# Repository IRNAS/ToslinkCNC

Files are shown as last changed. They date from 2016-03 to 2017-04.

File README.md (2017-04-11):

# ToslinkCNC

CNC machine is usually controlled via parallel bus, containing six signals. For each of the three axes there are two signals: STEP and DIR. At each positive edge of the STEP signal, the corresponding stepper motor moves into direction set by DIR signal. In addition to these six signals, there can also be other general purpose control signals.

Parallel bus on longer distances and in noisy environment can be susceptible to electromagnetic interferences. Because of this we decided to design an interface to transport these parallel signals via an optical link. For successful transfer via optical fiber the first thing that must be done is to convert parallel data to serial bit stream. Moreover, because of the inherent design of optical transmitters and receivers, serial data must also be Manchester encoded.

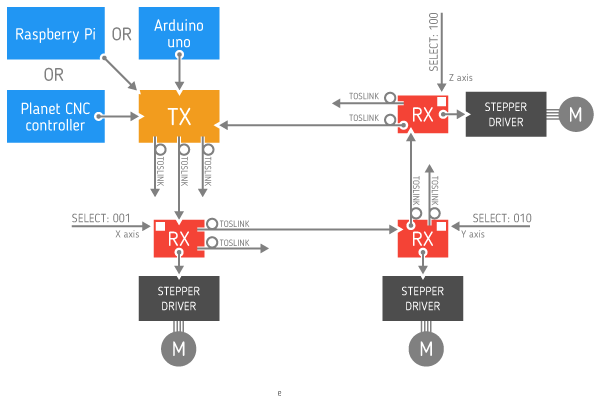
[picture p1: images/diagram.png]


Our design is based on [Serializer / Deserializer for Audio Fiber Optic](http://opencores.org/project,parallel_io_through_fiber) project published on Open Cores. 

## Use cases
ToslinkCNC has been developed for use with [GoodenoughCNC Plasma](http://goodenoughcnc.eu) cutter as our answer to continuous problems with electrical noise and interference. The following configuration is used in the system. 

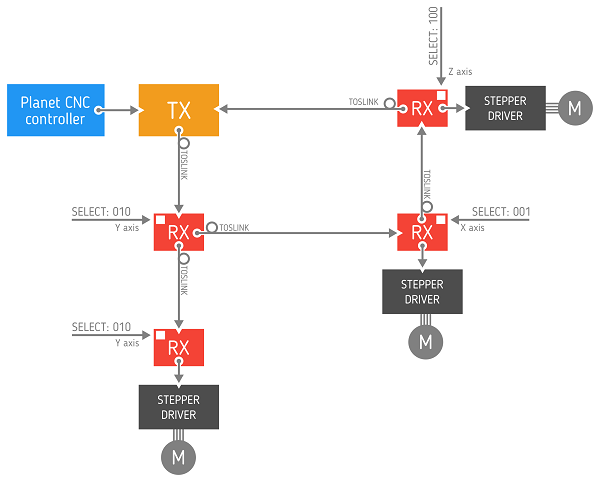
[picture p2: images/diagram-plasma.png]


## Toslink Receiver-transceiver

For each motor on the CNC machine there is one PCB, containing Toslink receiver. Receiver PCB, together with motor driver, can be mounted on the motor. Receiver is being used with [PoLabs' PoStep25-32 stepper motor driver](http://www.poscope.com/PoStep25-32). PCB is being powered through motor driver connector using +5V. To enable this the +5V supply from motor driver should be connected to unused 9th pin on the driver's IDC connector usign a piece of insulated wire. PCB consists of one CPLD, two optical transmitters, one optical receiver, one DIP switch for selecting the axis and one limit switch / trigger connector. Limit switch is insulated through an optocoupler and trigger output is open drain type. Toslink transmitter DLT1111 and Toslink receiver DLR1111 were used, which enable data transfer speed up to 16 Mbps. We used Xilinx XC9572XL CPLD to implement the necessary logic for protocol conversion. Receivers can also be connected in daisy chain.

### Using IDC-10 connector:
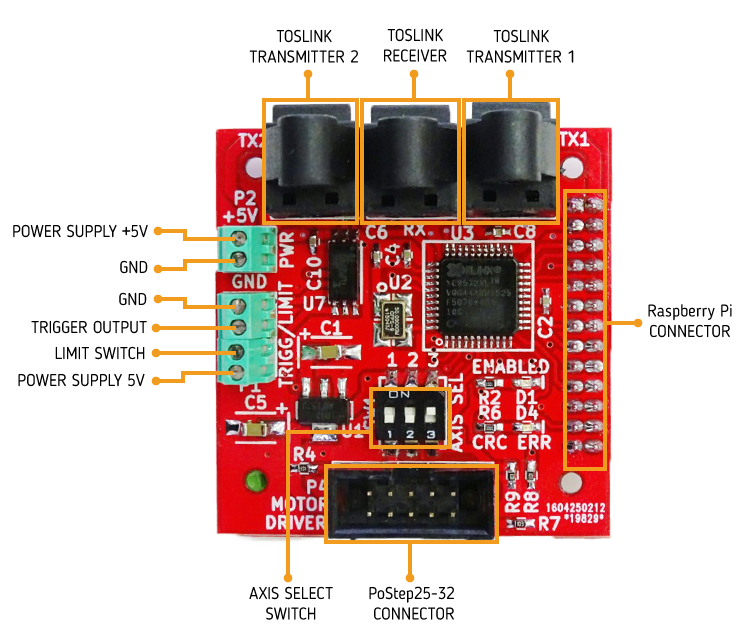
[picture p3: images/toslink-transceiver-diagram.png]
toslink-cnc-1


### Using terminal blocks:
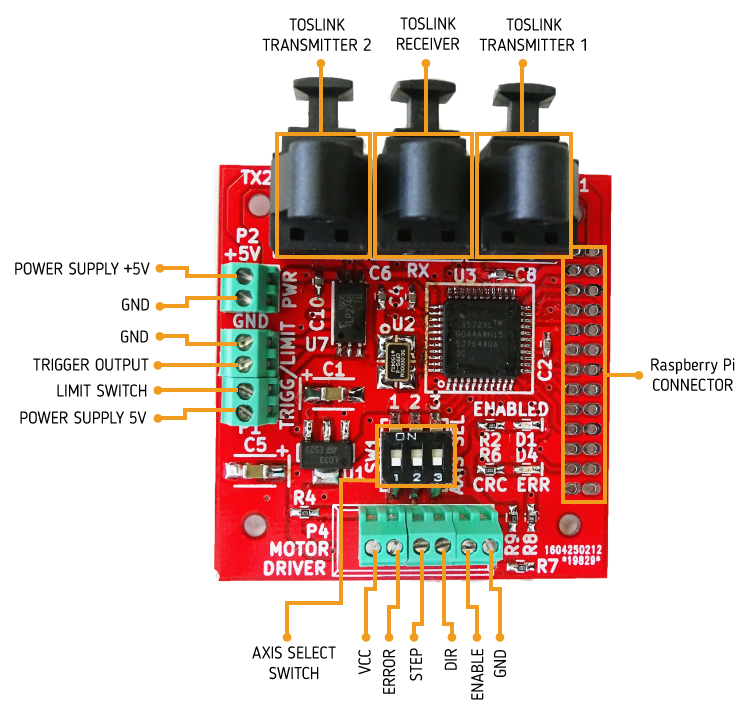
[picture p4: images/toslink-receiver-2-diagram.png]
toslink-cnc-1-1


## Toslink Transmitter

Transmitter consists of two PCBs, an Arduino sield and a Toslink transciever. Both PCBs are stacked together. Toslink transciever PCB is identical to one used for receiver. Arduino shield consists of headers for Arduino and connectors for [CNC USB Controller Mk3/4 from Planet CNC](http://www.planet-cnc.com/index.php?page=hardware) and PoStep25-32 driver. There is also a terminal block for connecting limit switches and trigger signals. Circuit can be powered either through terminal block (+5V), through Arduino Uno if attached as a shield, or from Planet CNC Controller.

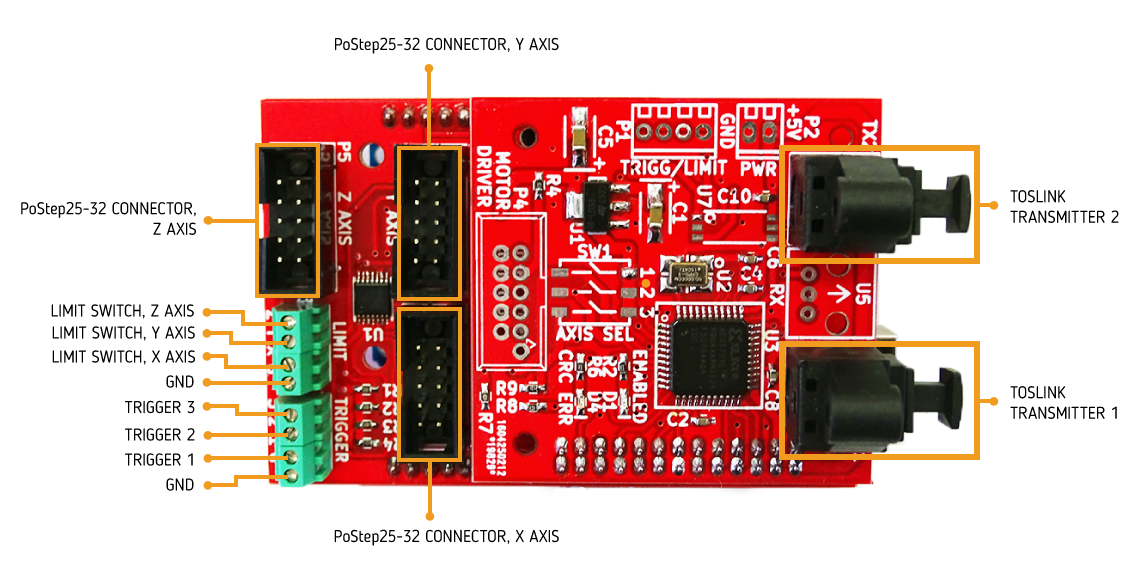
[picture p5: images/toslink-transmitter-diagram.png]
toslink-cnc-1-2


## Toslink Transmitter / Arduino Shield

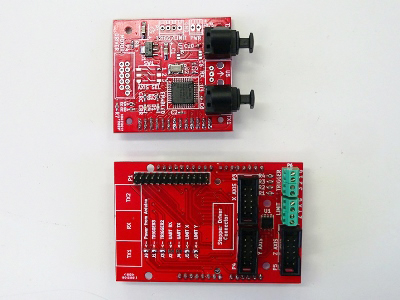
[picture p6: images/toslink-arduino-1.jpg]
toslink-cnc-2

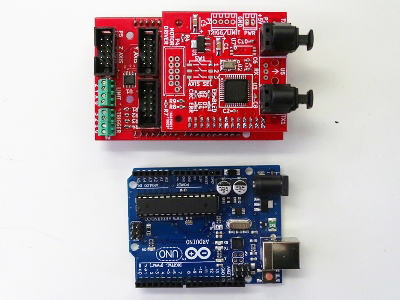
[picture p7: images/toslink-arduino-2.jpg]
toslink-cnc-3

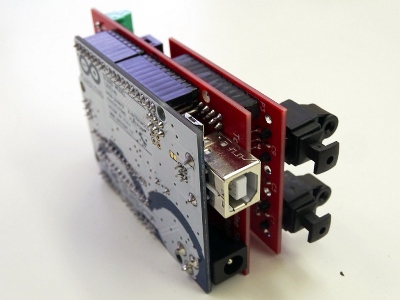
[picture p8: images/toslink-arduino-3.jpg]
toslink-cnc-4


## Toslink Transmitter / Planet CNC

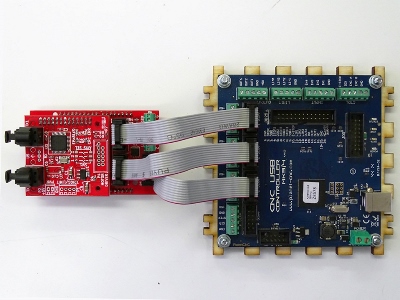
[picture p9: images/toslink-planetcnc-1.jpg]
toslink-cnc-5

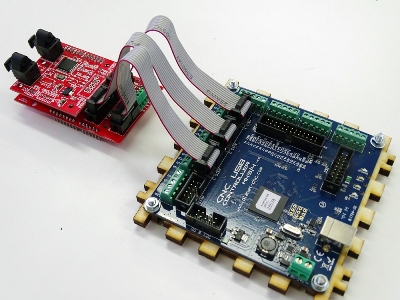
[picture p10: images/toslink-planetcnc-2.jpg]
toslink-cnc-6


## Toslink Transmitter / Raspberry Pi Shield

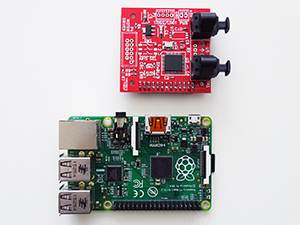
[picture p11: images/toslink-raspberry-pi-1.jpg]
toslink-cnc-7

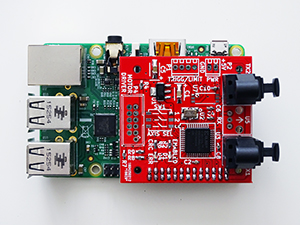
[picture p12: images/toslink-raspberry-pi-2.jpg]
toslink-cnc-8


## Firmware Description

All data is being transmitted in frames of fixed length. Frames are transmitted without gaps between them. Each frame contains 3 direction values, 3 step values, vaule of enable signal, 3 values of limit/end switch signals (these fields are being shared with 3 trigger values), parity bits and frame delimiter. To detect parity bit corruption, both even and odd parity bits are being transmitted. Transmitter places direction, step, enable and trigger values in new frame, adds calculated parity bits and sends the frame to the first receiver in daisy chain. Receiver reads the enable value and direction, step and trigger values ( based on axis selection). Receiver replaces the correspondig trigger value with limit switch value, calculates new parity bits and sends this new frame to the next receiver in dasy chain. Output of the last receiver in dasy chain is connected to transmitter input. Transmitter reads all three limit switch values from received frame.

frame-structure

Data in optical fiber is manchester encoded. For logic '0', logic '1' and frame delimiter three different patterns are being used. They were selected so that all of them have the same length and are completely different from each other. Decoding is based on time elapsed between two rising edges of clock. If elapsed time is shorter than 12 clock cycles, receiver decodes it as a short step. If it's longer than 12 and shorter than 20 clock cycles, then it's decoded as a medium step. If elapsed time is longer than 20 clock cycles, it's decoded as a long step.

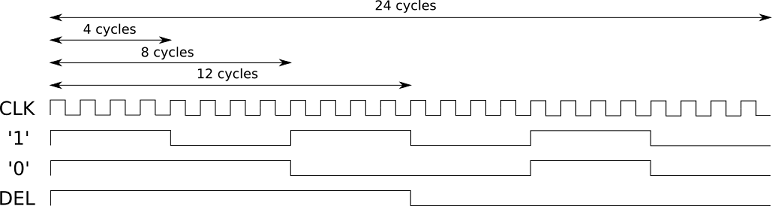
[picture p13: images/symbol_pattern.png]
symbol-pattern


Main transmitter module consists of a step sampler and an optical transmitter. Step sampler samples and shapes incomming step, direction, enable and trigger signals and passes them forward to the optical transmitter. Optical transmitter handles data framing, manchester encoding and sends encoded data to Toslink transmitter.

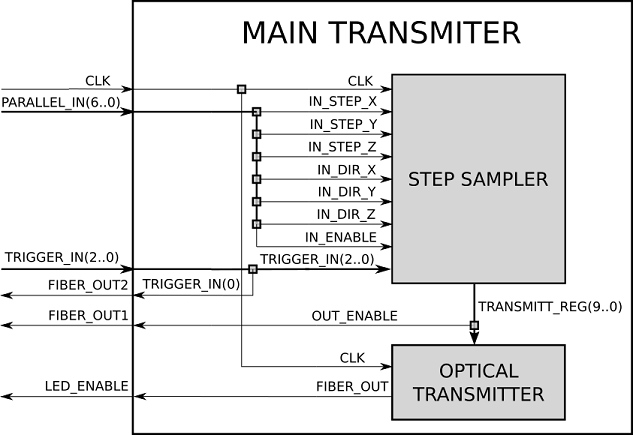
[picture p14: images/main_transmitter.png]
main-transmitter-module


Block diagram of step sampler is presented in figure below:

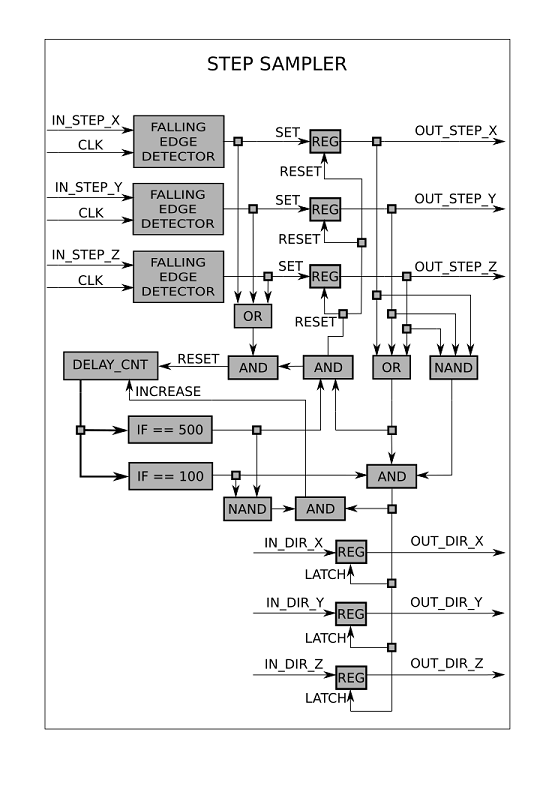
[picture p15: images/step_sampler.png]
step-sampler


Optical transmitter consists of shift register and manchester encoder. Shift register block diagram is presented in figure below:

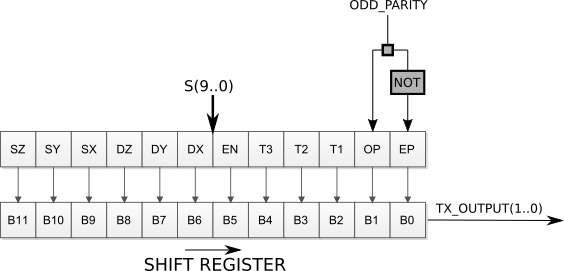
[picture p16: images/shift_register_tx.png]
shift-register-tx


Manchester encoder consists of three look-up tables and one multiplexer. If value of *tx_output* is "00" the '0' pattern, if  "01" the '1' pattern and if "10" the DEL pattern is generated on the output.

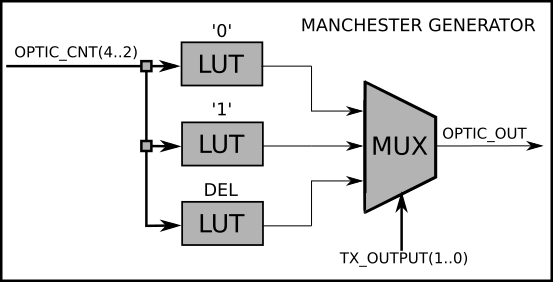
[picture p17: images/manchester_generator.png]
manchester-encoder


Main receiver module consists of an optical receiver and a step generator. Optical receiver accepts signal from Toslink receiver, decodes it and passes extracted data to step generator. It also adds limit signal values, calculates new parity, manchester encodes data and passes it foward to both Tolsink transmitters. Step generator correctly shapes the received signals.

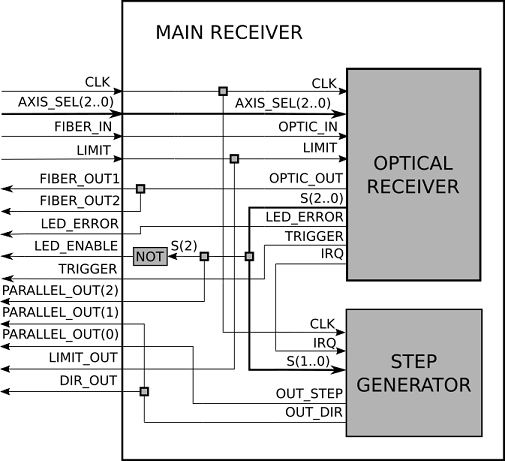
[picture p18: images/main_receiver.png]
main-receiver-module


Optical receiver consists of manchester decoder, shift register and manchester encoder (which is identical to the one used in transmitter). Block diagram of receiver shift register is presented in figure below:

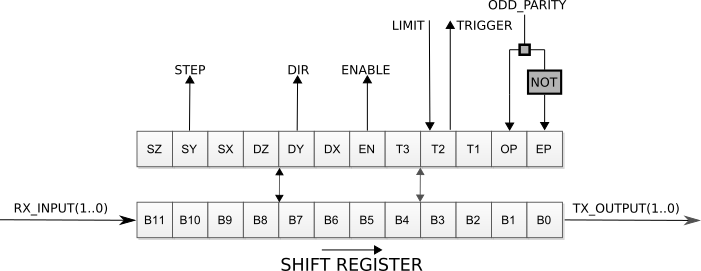
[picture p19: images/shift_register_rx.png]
shift-register-rx


Manchester decoder consists of a simple low-pass filter and a step sampler.

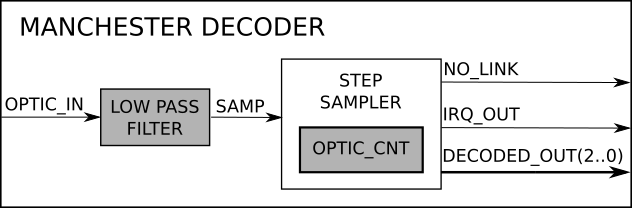
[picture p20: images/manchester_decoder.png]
manchester-decoder


Step sampler is a finite state machine. It's diagram of possible states is presented in figure below. Movement between states is based on received step width: short, medium or long. If step width is too long, the connection is lost and motor driver is disabled (enable signal equals to '1'). As soon as the correct manchester symbol is received, the connection is again established.

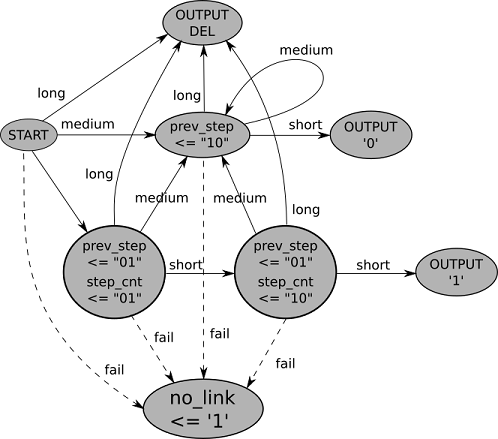
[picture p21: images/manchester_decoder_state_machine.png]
manchester-decoder-state-machine


## Known Isues

 * There is not enough room on the CPLD to hold both, the transmitter and the receiver. To enable transfer of limit switch signals from receivers back to transmitter, there would also need to be an additional optical receiver implemented on the transmitter PCB's CPLD. This problem can be solved by stacking two transcievers one over another. Firmware for the second transciever is available in [Transmitter](Transmitter/return path receiver CPLD VHDL code) folder.

---

#### License

All our projects are as usefully open-source as possible.

Hardware including documentation is licensed under [CERN OHL v.1.2. license](http://www.ohwr.org/licenses/cern-ohl/v1.2)

Firmware and software originating from the project is licensed under [GNU GENERAL PUBLIC LICENSE v3](http://www.gnu.org/licenses/gpl-3.0.en.html).

Open data generated by our projects is licensed under [CC0](https://creativecommons.org/publicdomain/zero/1.0/legalcode).

All our websites and additional documentation are licensed under [Creative Commons Attribution-ShareAlike 4 .0 Unported License] (https://creativecommons.org/licenses/by-sa/4.0/legalcode).

What this means is that you can use hardware, firmware, software and documentation without paying a royalty and knowing that you'll be able to use your version forever. You are also free to make changes but if you share these changes then you have to do so on the same conditions that you enjoy.

Koruza, GoodEnoughCNC and IRNAS are all names and marks of Institut IRNAS Rače. 
You may use these names and terms only to attribute the appropriate entity as required by the Open Licences referred to above. You may not use them in any other way and in particular you may not use them to imply endorsement or authorization of any hardware that you design, make or sell.

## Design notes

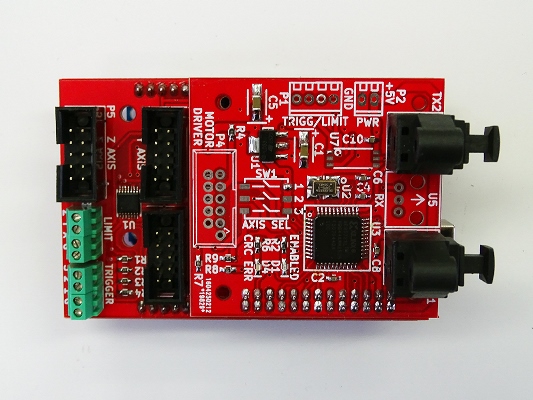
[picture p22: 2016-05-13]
images/transmitter-pinout.jpg

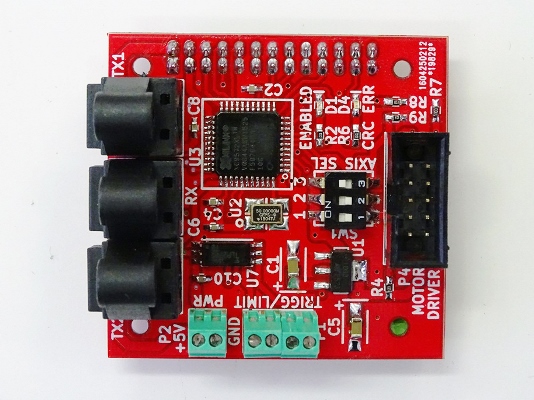
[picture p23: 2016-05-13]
images/transceiver-pinout.jpg

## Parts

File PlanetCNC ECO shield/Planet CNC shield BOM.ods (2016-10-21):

Designator | Package | Quantity | Description
P1 | Toslink CNC Transciever | 1 | Toslink CNC Transciever
P2 | Planet CNC ECO | 1 | Planet CNC ECO
P3 | terminal block, 2.5mm, 2-pole | 1 | term block 2

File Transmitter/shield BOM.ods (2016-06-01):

Designator | Package | Quantity | Description
P2 | Toslink CNC Transciever | 1 | Toslink CNC Transciever
P1 | Arduino UNO | 1 | Arduino UNO
P3,P4,P5 | male IDC 10 | 3 | PoStep25-32 connector
P6,P7 | terminal block, 2.5mm, 4-pole | 2 | term block 4
R1,R2,R3,R4 | R0603 | 4 | 10K

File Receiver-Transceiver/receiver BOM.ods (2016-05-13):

Designator | Package | Quantity | Description
P3 | female header straight, 2x13, 2.54mm | 1 | RPI header
P4 | male IDC 10 | 1 | PoStep25-32 connector
U4,U6 | DLT1111 | 2 | Toslink transmitter
U5 | DLR1111 | 1 | Toslink receiver
U3 | VQFP44 | 1 | XC9572XL
U1 | SOT-223 | 1 | TLV1117, 3.3V
C9,C8,C7,C6,C4,C3,C2,C10 | C0603 | 8 | 100nF,25V
C5,C1 | tantal capacitor, size B | 2 | 10uF,25V
U2 | TCXO 5x3.2 mm | 1 | CFPS-9-50M, 50MHz
D1 | LED 0603 | 1 | LED Green SMD
R2,R6,R1 | R0603 | 3 | 1K
D4 | LED 0603 | 1 | LED Red SMD
R7,R8,R9,R3,R4,R5 | R0603 | 6 | 10K
P1 | terminal block, 2.5mm, 4-pole | 1 | term block 4
Q1 | SOT-23 | 1 | RSR010N10FHATL
U7 | SO6L, optocoupler | 1 | TLP2704
P2 | terminal block, 2.5mm, 2-pole | 1 | term block 2
SW1 | DIP switch | 1 | A6S-3102-H

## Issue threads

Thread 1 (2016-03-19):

why  optical link?!

mkeyno, 2016-03-19:
hi
why do you use the complex  optical link  where as there is couple of robust wireless links such as old one Bluetooth and new one ESP8266,?also there is couple of modify Marlin for laser and plasma cutting
BR

SloMusti, 2016-03-19:
Plasma cutters and laser cutters generate high voltage and a lot of RF noise, thus jamming Bluetooth or WiFi, which is not great anyhow for robust and reliable real-time communication, which is required on CNC machine to have all motors synchronised.

mkeyno, 2016-03-19:
hi@SloMusti , good experience, I didn't know , however I make laser machine with 120 watt laser tube and HC-06 for witless link connection  , till now its work perfectly , but for plasma I don't have any experience, actually I've plan to use modified Marlin in my next  plasma machine and find many cool guys here make very good wireless serial bridge , do you think is there way to keep the noise away from the broad? the ESP module so tempting even @openhardwarecoza make leserweb interface can be embedded in the ESP flash, so you need nothing just connect the ESP

openhardwarecoza, 2016-03-19:
Ps you should check my progress on Laserweb2.0 (: i built a plasma too,
running smoothieware. Busy adding toolpath offset to laserweb2 to
compensate for the kerf on my plasma
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

openhardwarecoza, 2016-03-19:
See https://plus.google.com/collection/UbVXZB
On 19 Mar 2016 16:21, "Peter van der Walt (Gmail)" <
peter.plaaswerf@gmail.com> wrote:

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

openhardwarecoza, 2016-03-19:
Sorry,  more direct link:
https://plus.google.com/+PetervanderWalt/posts/Mv5Je3um89u
On 19 Mar 2016 16:22, "Peter van der Walt (Gmail)" <
peter.plaaswerf@gmail.com> wrote:

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
>>> hi@SloMusti , good experience, I didn't know , however I make laser
>>> machine with 120 watt laser tube and HC-06 for witless link connection ,
>>> till now its work perfectly , but for plasma I don't have any experience,
>>> actually I've plan to use modified Marlin in my next plasma machine and
>>> find many cool guys here make very good wireless serial bridge , do you
>>> think is there way to keep the noise away from the broad? the ESP module so
>>> tempting even @openhardwarecoza <https://github.com/openhardwarecoza>
>>> make leserweb interface can be embedded in the ESP flash, so you need
>>> nothing just connect the ESP
>>>
>>> —
>>> You are receiving this because you were mentioned.
>>> Reply to this email directly or view it on GitHub
>>> <https://github.com/IRNAS/ToslinkCNC/issues/1#issuecomment-198710186>
>>>
>>

SloMusti, 2016-03-19:
@openhardwarecoza  LaserWeb looks great, we will definitely try it out with ToslinkCNC and Arduino running Grbl or Marlin, we were after solution like yours for a while.

Bluetooth/WiFi is an option, however having it operate reliably in workshop environments for real-time transmission can be a problem. Note that the wireless bridge between computer and controller is ok, because communication is buffered at the controller. Toslink CNC is different however, since it is the connection between the controller and stepper drivers themselves. Thus we can have the controller sufficiently far away from the machine. To that point you can have also a wireless RF link is need be, but might as well have it connected to the computer.

openhardwarecoza, 2016-03-19:
I like the optical idea.  (i have a 40a GF start chinese plasma)
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

openhardwarecoza, 2016-03-19:
Gf = hf
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

SloMusti, 2016-03-19:
You are definitely in need of an optical system or serious shielding. We had even 3D printers running Marlin about 5m from plasma arc failding from its noise and have since purchased a Telwin cutter, that has internal start in the cutting head.

openhardwarecoza, 2016-03-19:
It's not quite that bad.  Using drag cut for the start cuts down a lot of
the HF noise.  And i have success with the machine 1.5m away from my
laptop.  But i do admire this project's idea.  Any hack that reuses off the
shelf products gets my vote (easy to source)

Video (old,  now a days i cut a lot closer to the material) :
https://youtu.be/0ZMn9tS2_II

My bigger gripe is to get smoothieware to pause and wait for an Arc OK
(building a thc/arc ok is easy,  interfacing to mach is easy.  Interfacing
thc/arc ok to one  og the firmwares,  not easy.
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

SloMusti, 2016-03-19:
Sure, under normal cut and drag start is ok. As soon as you screw up something or cut across a hole, the problem begins. This could be hacked by modifying plasma cutter to have HF active only on trigger for a few seconds. But generally I dont want to have people digging up cutters.

We have went as far as to have an opto triggered relay at plasma-cutter that triggers it and an experimental system for torch height control, where an LED is powered via a resistor divider from the arc voltage itself, coupled into fibre and then optical amplitude measured far away. Works reasonably well but needs some more playing with. Would be nice if Marlin had a THC software module and just used an ADC for input with a fibre measurement system like this or using an i2c ambient light sensor to read the voltage.

There are a few more options how to go about this,

SloMusti, 2016-03-19:
@openhardwarecoza Could you maybe use some pause signal or something like that. Or reusing rpm control if any is present, since spindles take some time to ramp up and some firmwares support it. Not sure if Marlin or similar does.

openhardwarecoza, 2016-03-19:
We are working on adding it to smoothie.  I am avoiding marlin like the plague.  Just too slow, and the codebase too messy

openhardwarecoza, 2016-03-19:
Reusing the temperature wait: https://github.com/Smoothieware/Smoothieware/issues/841

mkeyno, 2016-03-19:
hi @SloMusti , there is couple of guys such as @HakanBastedt who's working new version of marlin for cutting machine like laser , I discuss with him about how to use special pin state to check readiness of tools (in this case plasma torch) before any command process . I saw in many industrial plasma & laser  machine tools readiness, ( in laser auto focus system and in plasma THC system ) work independently, whereas in Marlin , it is possible to bind   this feature in loop function, I believe one of the big missing part of many open source is to presume the tools is always ready , I hope @openhardwarecoza peter could spare more time for such project

SloMusti, 2016-03-19:
@mkeyno agreed on that, we see this need as well and would be nice to figure out the workflow for open hardware/software machines such they are simple and reliable enough for all use-cases and sufficiently user friendly. Currently we are working towards completing the http://goodenoughcnc.eu/ range of machines and the organized and simple control documentation will then be the missing part.

mkeyno, 2016-03-19:
good luck for that @SloMusti ,I'm following you and I suggest take time to review guys like @openhardwarecoza  and @luc-github work , they are making the last chain of integrated software/hardware embedded device for CNC machine , just connect the machine and start CAD-CAM and printing

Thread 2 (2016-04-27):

Clone axis or multiple axis.

Jmjcoke, 2016-04-27:
Hello,

I have built a machine that has X1-X2 and Y1-Y2 then Z. Instead of cloning can I just add rX card with same address for X1-X2 and Y1-Y2? How much trouble will it be to get the limit switches through the toslink? How do I add needed hardware to make switches work?

SloMusti, 2016-04-27:
You can have as many RX cards (Receiver-Transceiver) with the same address as you need, so your setup is perfectly feasible.

There is support for limit switches, every RX card has one input (limit) and one output (spindle enable or similar). Note that we have implemented this features just recently and will be releasing the new versions after testing in a week or two.

SloMusti, 2016-05-23:
@Jmjcoke please check out the new version now

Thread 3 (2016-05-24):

Not enough room on the CPLD to hold both, the transmitter and the receiver.

MatejGomboc, 2016-05-24:
There is not enough room on the CPLD to hold both, the transmitter and the receiver. To enable transfer of limit switch signals from receivers back to transmitter, there would also need to be an additional optical receiver implemented on the transmitter PCB's CPLD. This problem can be solved by stacking two transcievers one over another. Firmware for the second transciever is currently under development.

MatejGomboc, 2016-06-01:
Firmware for the second transciever is available in [Transmitter](Transmitter/return path receiver CPLD VHDL code) folder.

Closed 2016-06-03.

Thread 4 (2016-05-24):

Trigger signal inputs on transmitter need additional pull-up or pull-down resistors.

MatejGomboc, 2016-05-24:
Trigger signal inputs on transmitter need additional pull-up or pull-down resistors. It is an issue only if transmitter board is disconnected from Arduino, Raspberry PI or Planet CNC controller.

MatejGomboc, 2016-06-01:
Arduino shield has been updated. Pull-down resistors for Trigger1, Trigger2, Trigger3 and pull-up resistor for Enable were added.

Closed 2016-06-03.

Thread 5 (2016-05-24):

Axis other than xyz?

Jmjcoke, 2016-05-24:
Can I route x,y,z thru toslink and then route an extruder axis directly to the stepper drive or will there be axis synchronization problems?

SloMusti, 2016-05-24:
You can route the extruder independently of toslink, there will be a slight 5us delay, but that generally should have no effect on the machine operation at a hobby scale.

Jmjcoke, 2016-05-24:
Hobby scale? I am building a printer with a 1500mm Y axis, 800mm dual X
carriage, 900mm Z axis. I am going to wait until the firmware for a stacked
tx card is done. I think I can get the second X axis to run thru the second
card if the timing between the cards is synced.

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

SloMusti, 2016-05-24:
For a 3D printer, the possible synchronization error between motors and extruder can be neglected, because you have more variance in the plastic extrusion so a few us delay can not be noticed.

Lets assume Hobby scale as machines which move with speeds less then 10m/s and have precision less then 1um or similar, this is very vague, but applies to most machines at reasonable cost.

Timing between the cars is synced, so you can use it as it is already.

Jmjcoke, 2016-05-24:
Ok, 1um is small. I am good with 100-150 microns if I am lucky. I will let
you know. I have access to a API XD6 at work, I know it is overkill but it
will be fun to see how close it is.

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

--
Joshua Coke

815-708-1281

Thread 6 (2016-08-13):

Instructions

Jmjcoke, 2016-08-13:
Do you have detailed instructions on how to load firmware and get this system working?

SloMusti, 2016-08-14:
You can program the boards using XSVF player software for a number of programmers.

We use: http://dangerousprototypes.com/docs/Bus_Pirate_JTAG_XSVF_player
Also possible with Arduino: https://github.com/sowbug/JTAGWhisperer

Flashcat programmer you have supports XSVF programming as well based on the specs here: http://www.embeddedcomputers.net/products/FlashcatUSB/

You need to switch to JTWG mode and select the XSVF file, then program it.

Pick the firmware:
trasnceiver:  https://github.com/IRNAS/ToslinkCNC/blob/master/Receiver-Transceiver/receiver%20CPLD%20VHDL%20code%20%28all%20axes%29/toslink_receiver_all.xsvf
receiver: https://github.com/IRNAS/ToslinkCNC/blob/master/Transmitter/transmitter%20CPLD%20VHDL%20code/toslink_transmitter.xsvf

and program the board.

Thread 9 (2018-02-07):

Endstops yellow pcb

Luchador1981, 2018-02-07:
Hi i get my set with a yellow PCB 2 optical connectors one marked with TX and on with RX means that i have a send and reciving ? so i can use the 2 pins for the endstops on the toclinK PCB ?
( sorry for the wuestion i buy a long time ago but too many work to start with this project)

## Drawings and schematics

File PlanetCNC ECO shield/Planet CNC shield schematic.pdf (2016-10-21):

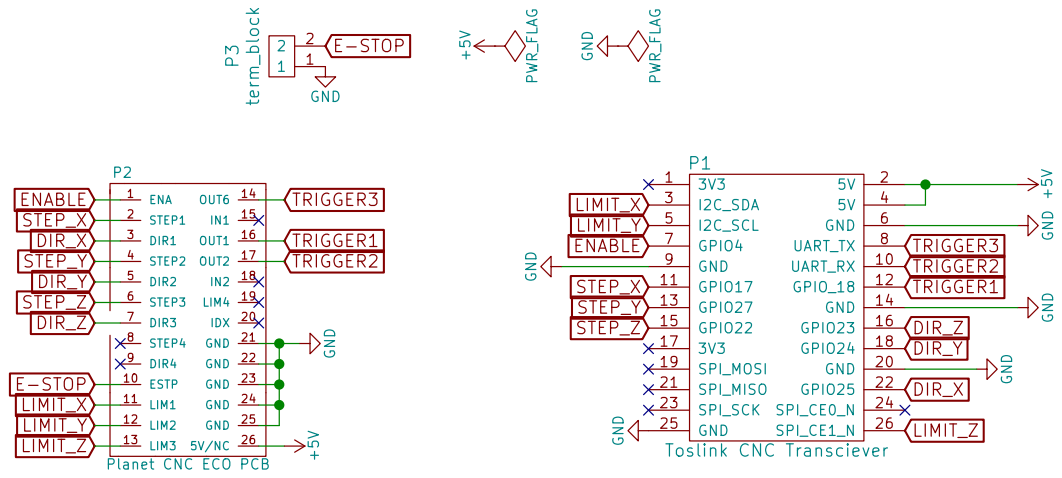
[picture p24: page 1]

LIM4 19 P2Planet CNC ECO PCB ENABLE

Institute IRNAS Rae
File: Toslink PlanetCNC ECO shield.sch Sheet: /
Id: 1/1 Title: Toslink CNC To Planet CNC ECO Shield

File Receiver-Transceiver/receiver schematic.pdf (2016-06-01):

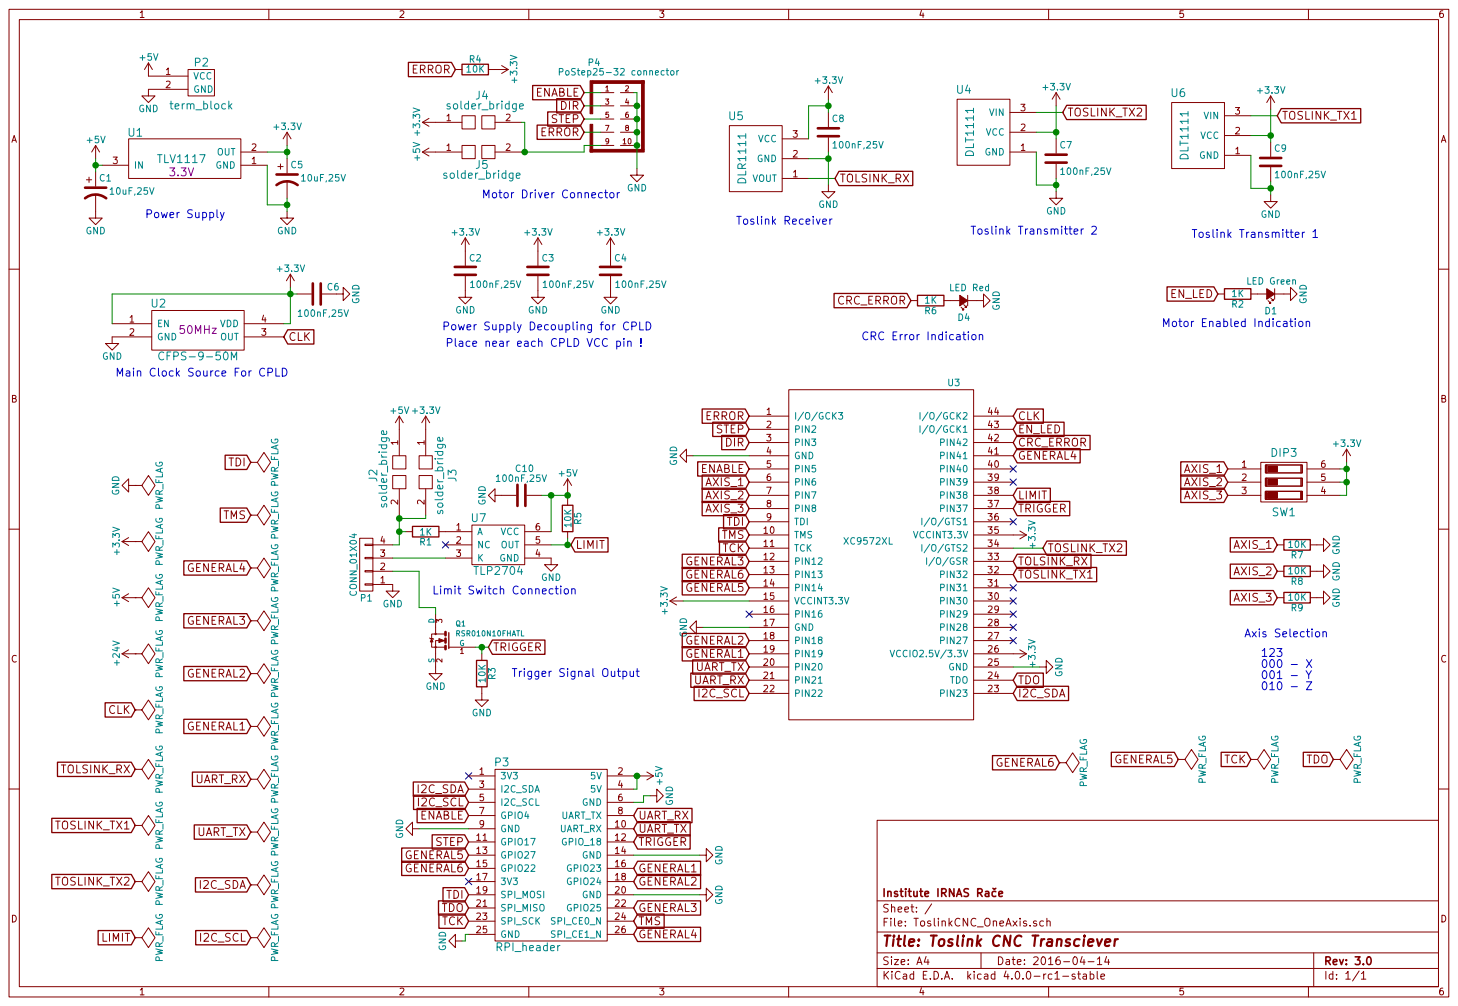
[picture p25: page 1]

Axis Selection Motor Enabled Indication CRC Error Indication Place near each CPLD VCC pin !

Main Clock Source For CPLD

4 P1 CONN_01X04

Institute IRNAS Rae
File: ToslinkCNC_OneAxis.sch Sheet: /
Id: 1/1 Title: Toslink CNC Transciever

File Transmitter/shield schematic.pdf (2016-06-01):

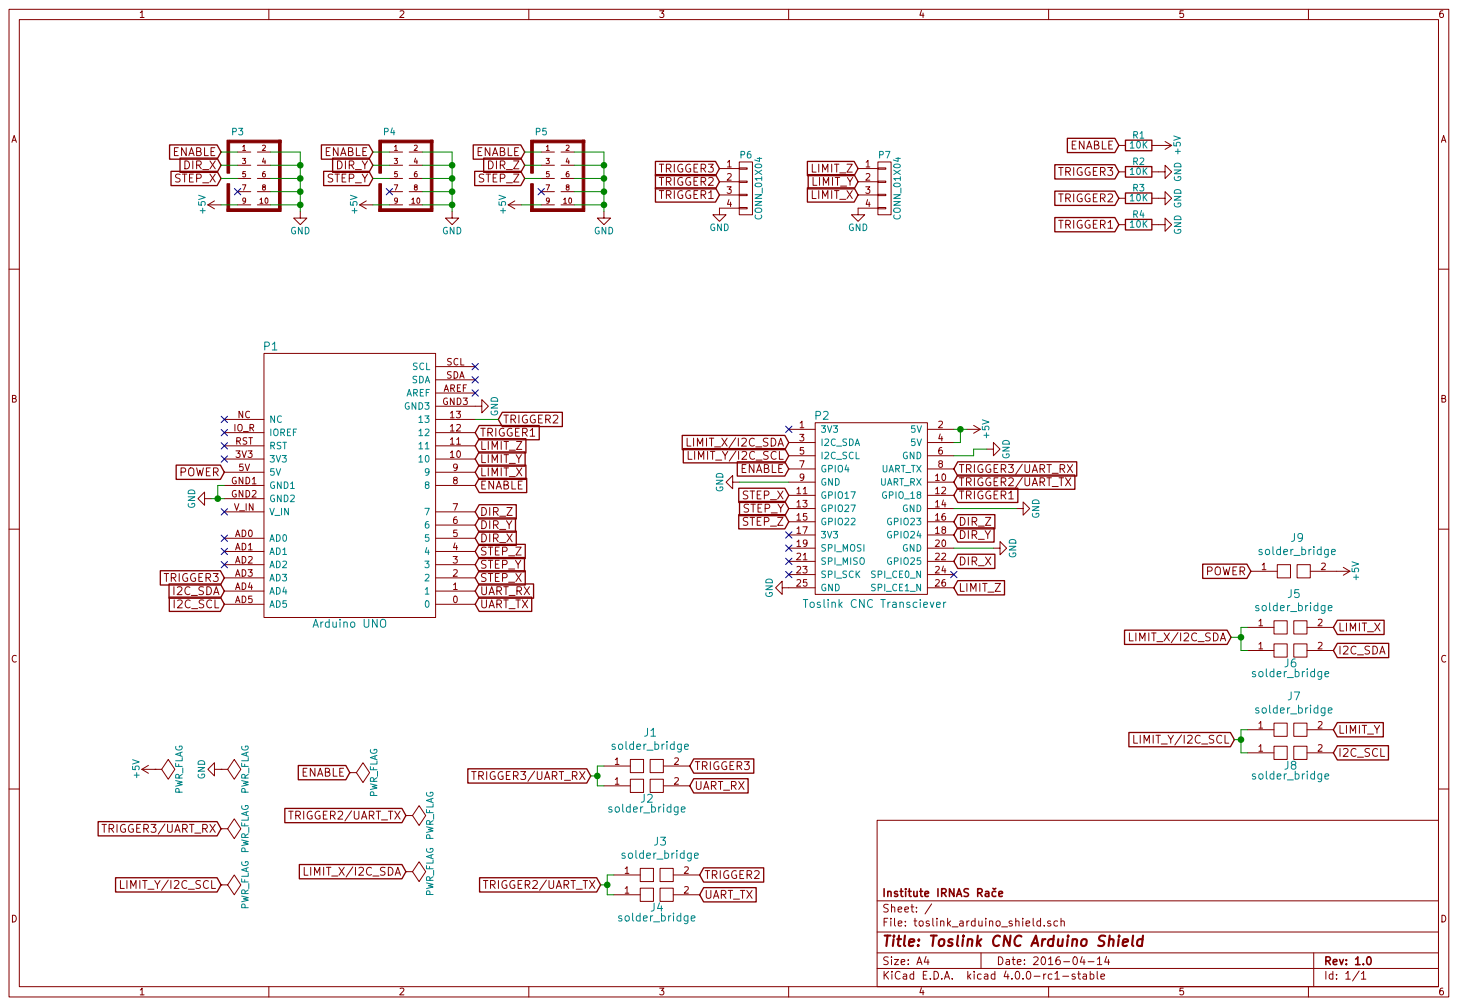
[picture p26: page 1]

Institute IRNAS Rae
File: toslink_arduino_shield.sch Sheet: /
Id: 1/1 Title: Toslink CNC Arduino Shield

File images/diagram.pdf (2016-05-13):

TX
RX

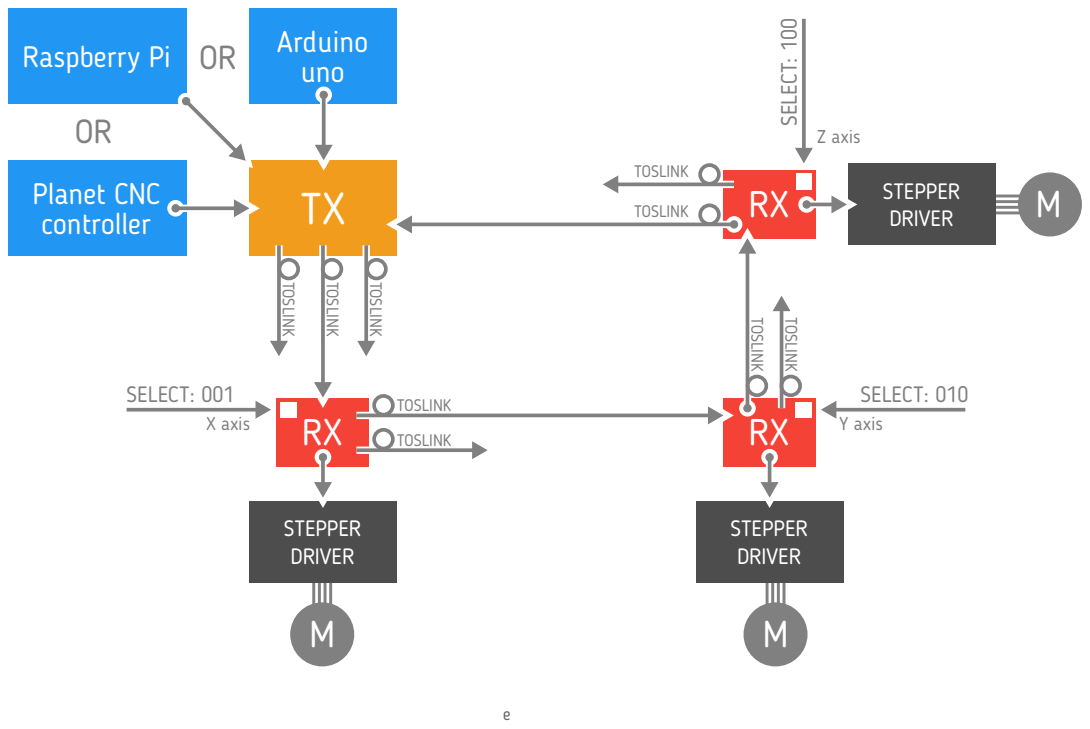
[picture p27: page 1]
STEPPER DRIVER; Arduino uno; TOSLINK; X axis; Y axis; Z axis; SELECT: 001; SELECT: 010; SELE

Raspberry Pi OR
Planet CNC
controller

Except where otherwise noted, this work is licensed under
http://creativecommons.org/licenses/by-sa/3.0/

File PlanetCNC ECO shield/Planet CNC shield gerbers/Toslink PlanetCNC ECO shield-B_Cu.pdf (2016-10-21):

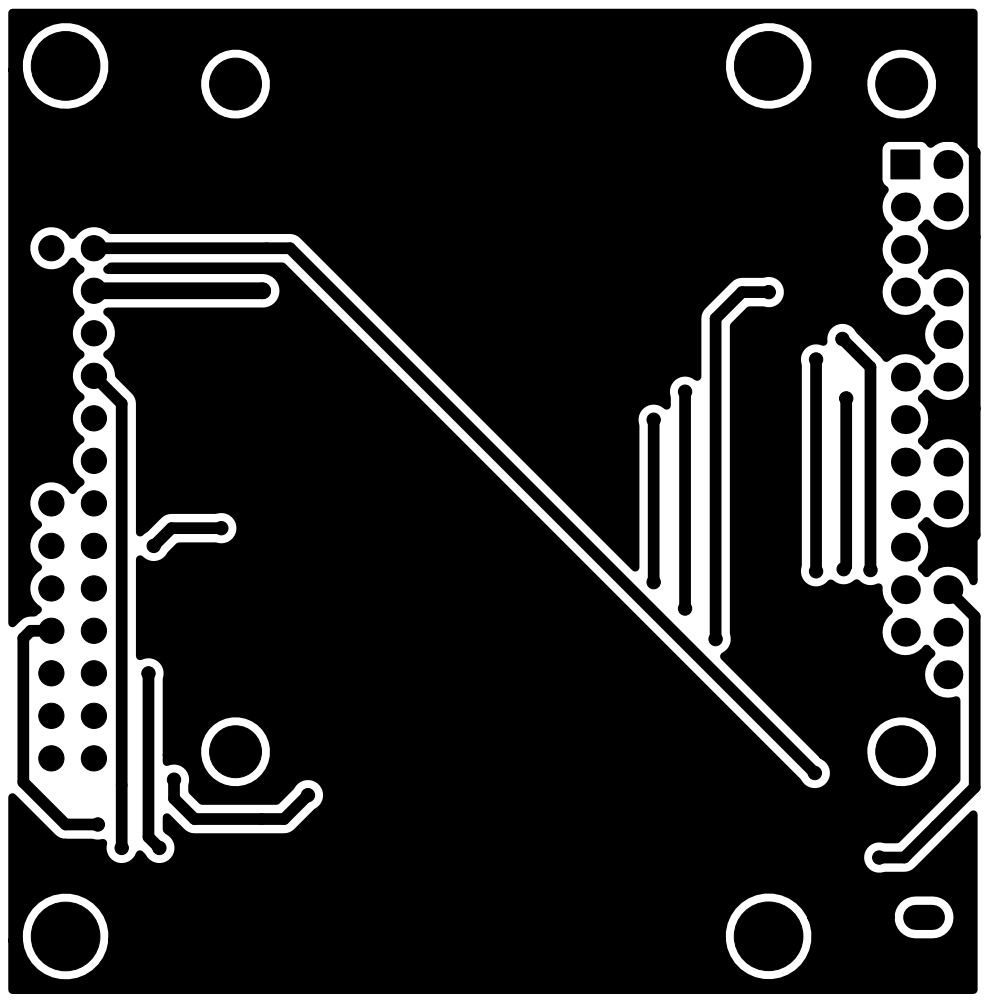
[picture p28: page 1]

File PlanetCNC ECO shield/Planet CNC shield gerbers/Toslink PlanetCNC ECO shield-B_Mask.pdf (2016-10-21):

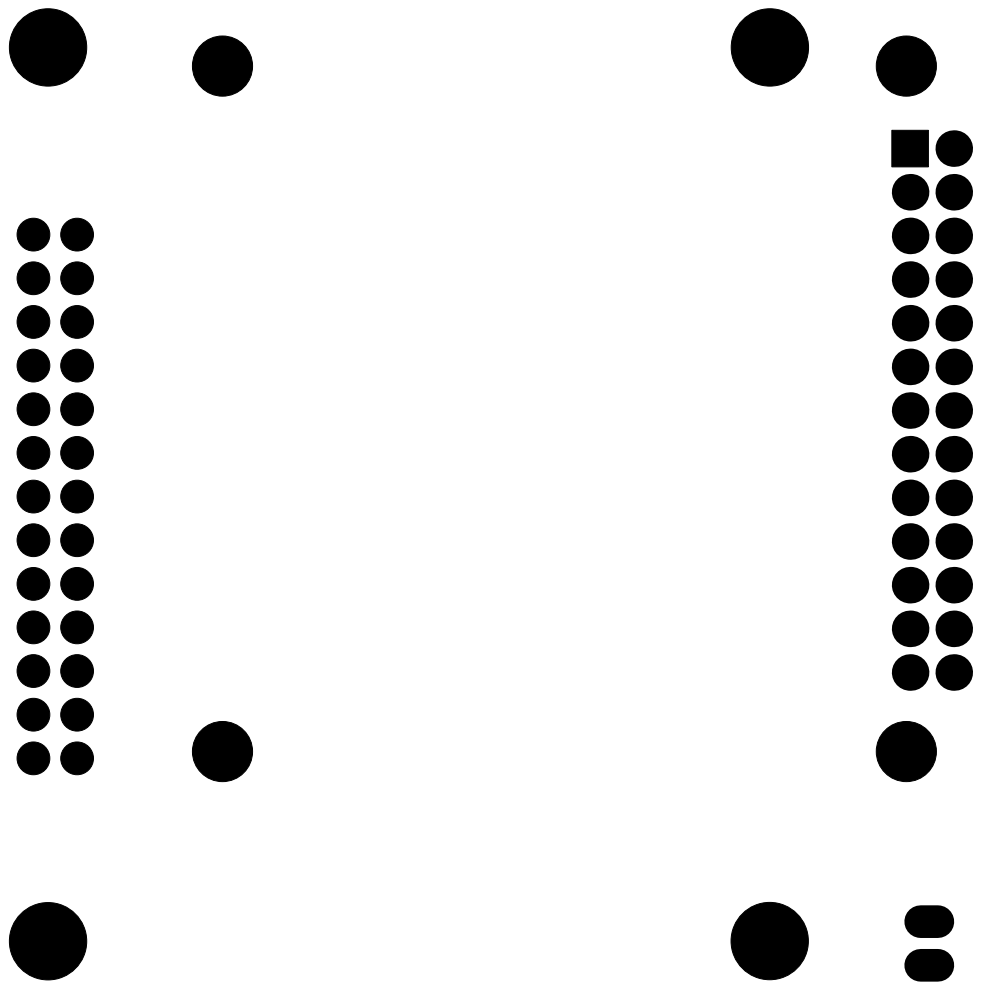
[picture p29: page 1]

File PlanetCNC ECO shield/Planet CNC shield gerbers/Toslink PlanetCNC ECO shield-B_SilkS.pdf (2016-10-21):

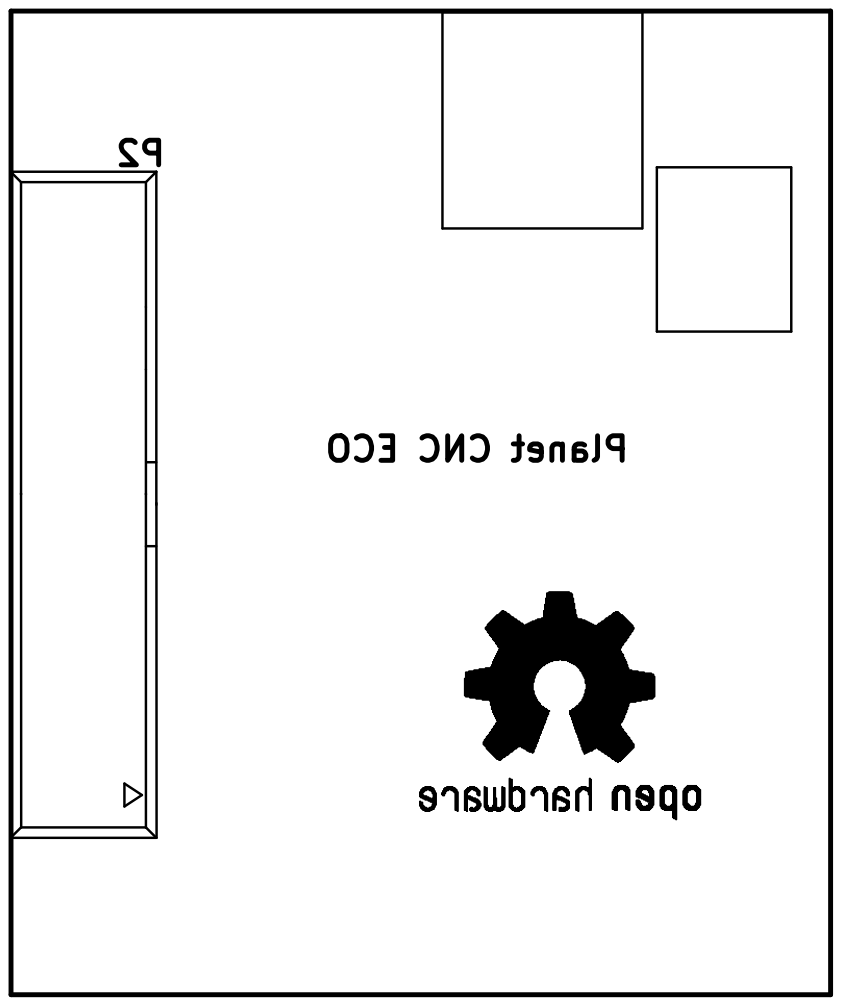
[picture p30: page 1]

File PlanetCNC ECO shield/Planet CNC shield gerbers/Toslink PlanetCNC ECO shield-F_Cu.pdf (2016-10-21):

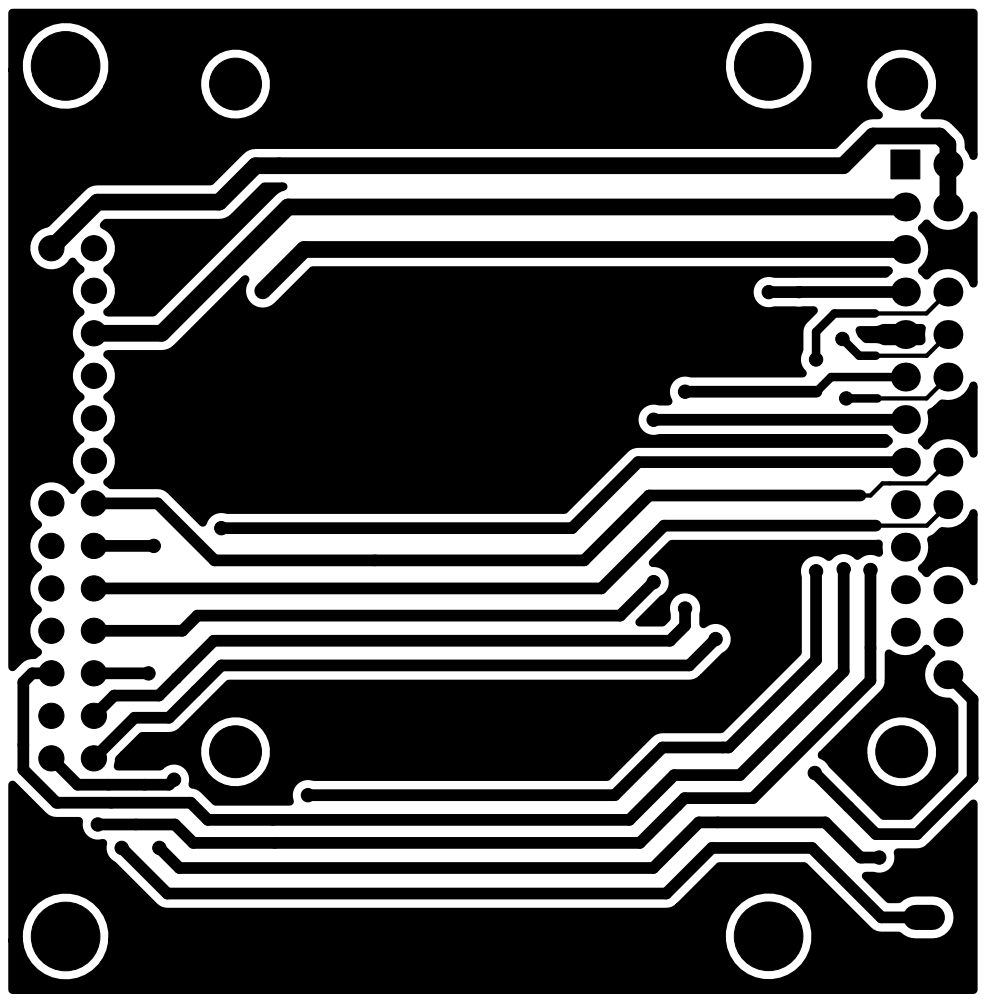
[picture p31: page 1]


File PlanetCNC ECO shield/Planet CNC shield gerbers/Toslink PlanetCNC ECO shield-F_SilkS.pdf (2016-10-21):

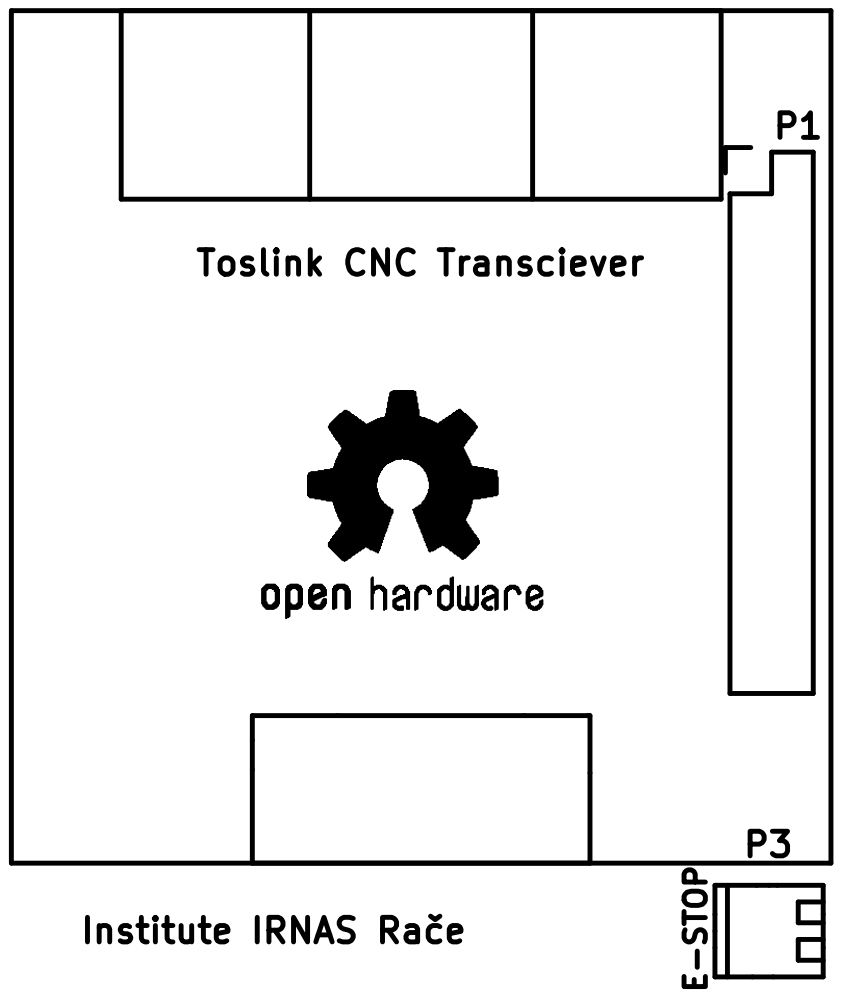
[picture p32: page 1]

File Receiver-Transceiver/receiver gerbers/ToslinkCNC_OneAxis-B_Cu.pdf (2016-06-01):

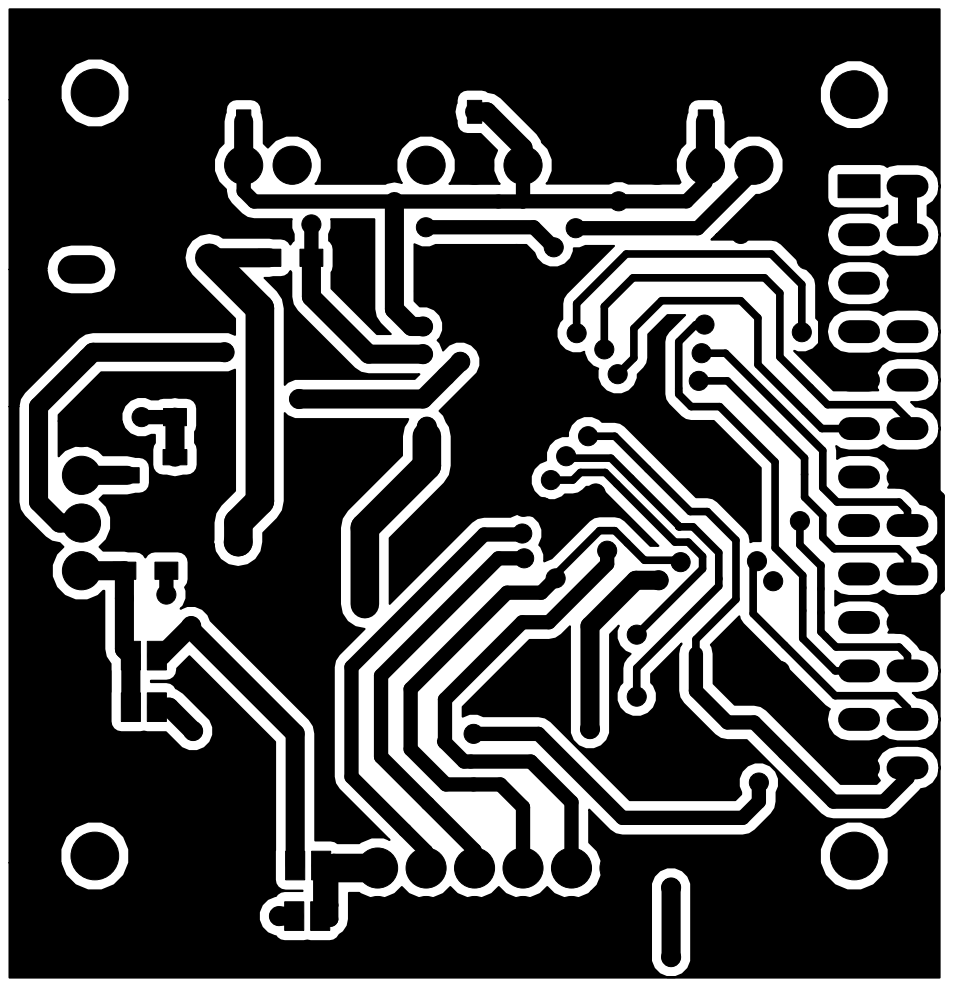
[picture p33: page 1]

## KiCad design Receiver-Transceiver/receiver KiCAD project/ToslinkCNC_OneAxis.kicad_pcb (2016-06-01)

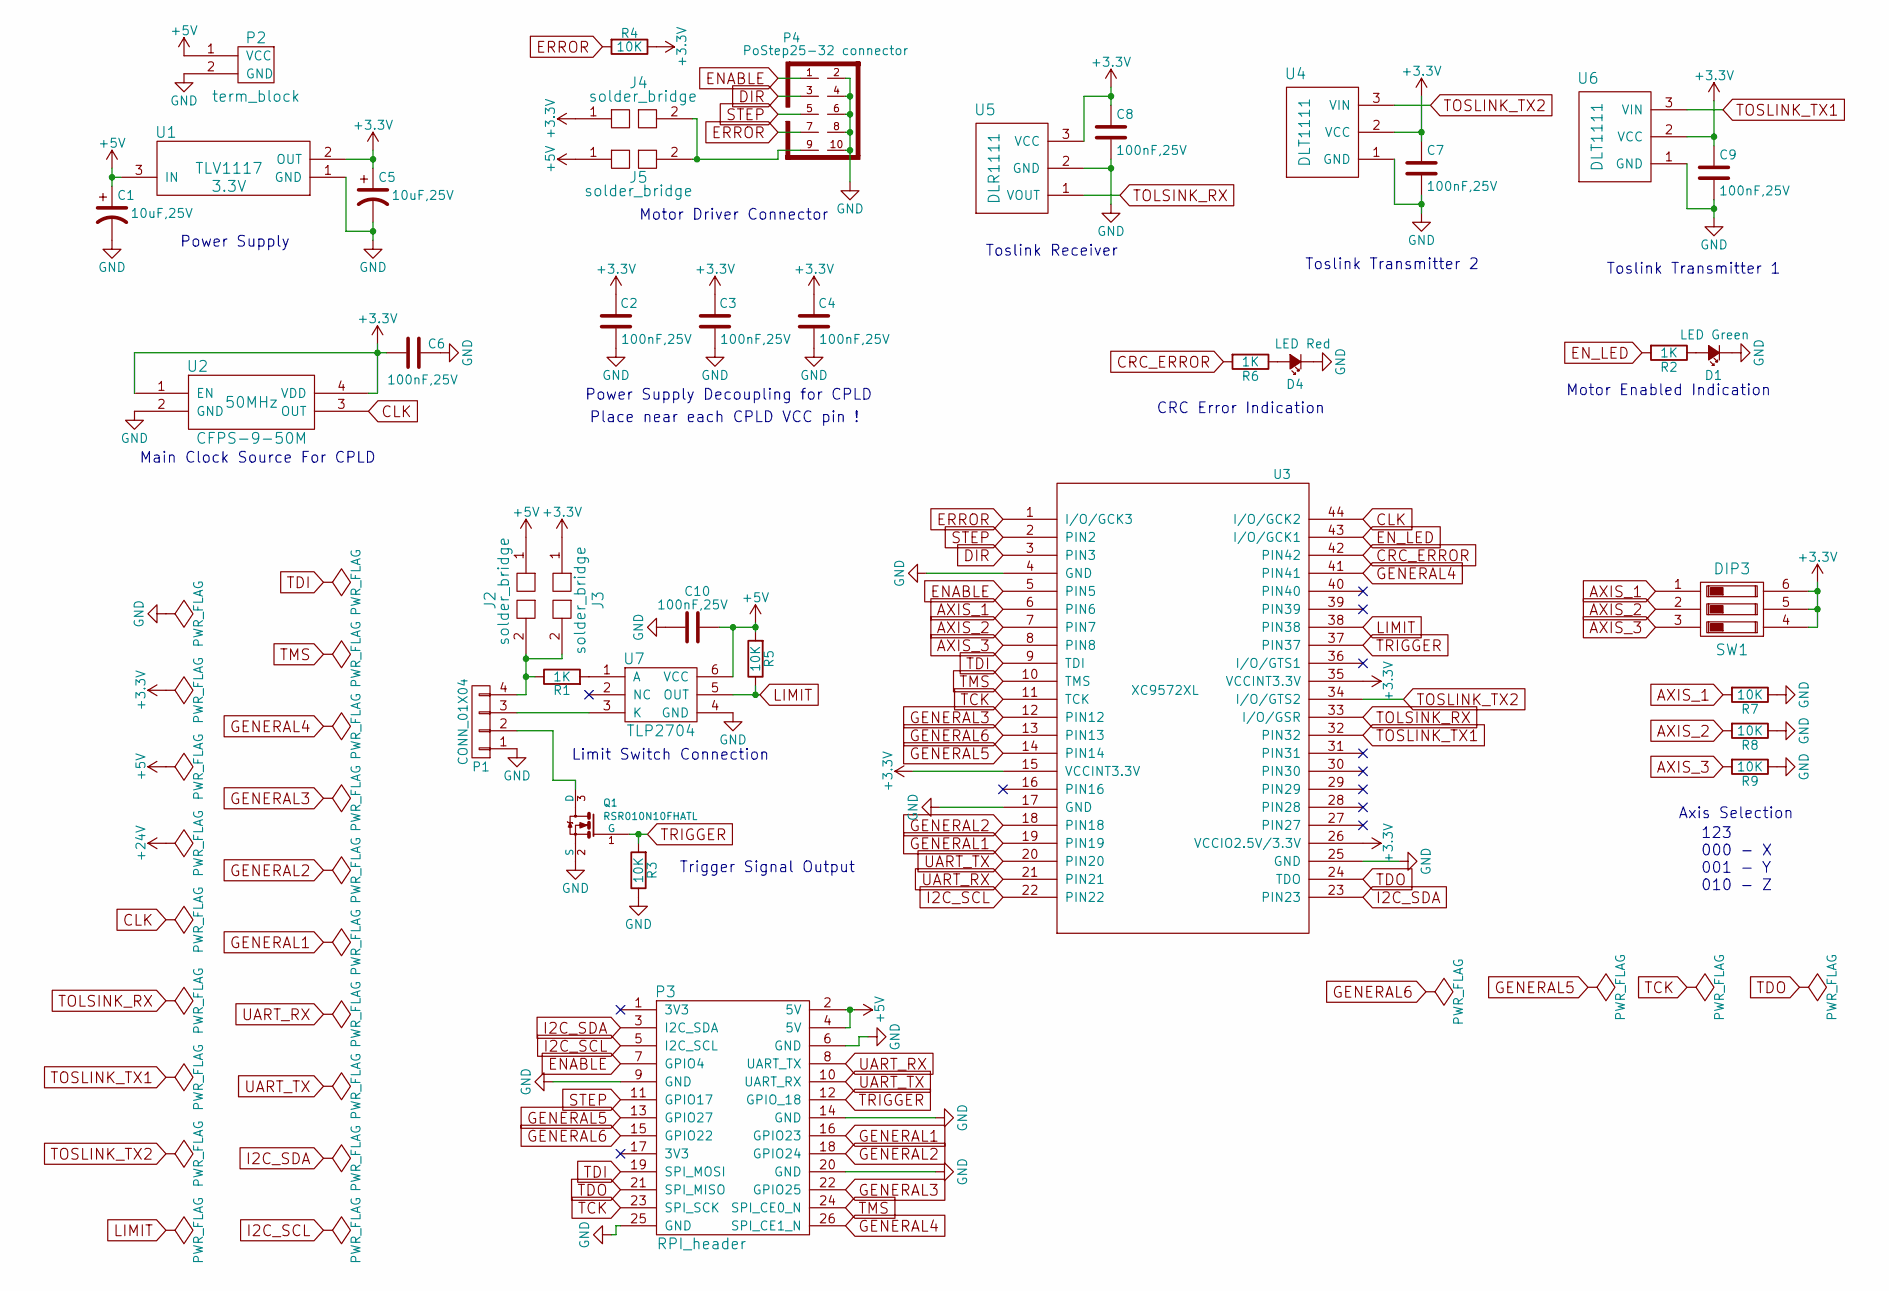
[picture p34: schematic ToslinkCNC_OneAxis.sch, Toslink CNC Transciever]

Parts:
C1, C5: 10uF,25V; TantalC_SizeB_EIA-3528_HandSoldering
C2, C3, C4, C6, C7, C8, C9, C10: 100nF,25V; C_0603_HandSoldering
D1: LED Green; LED_0603_HandSoldering
D4: LED Red; LED_0603_HandSoldering
J2, J3, J4, J5: solder_bridge
P1: CONN_01X04; terminal_block_2_5mm_4pole
P2: term_block; terminal_block_2_5mm
P3: RPI_header; Pin_Header_Straight_2x13
P4: PoStep25-32 connector; VASCH5x2
Q1: RSR010N10FHATL; SOT-23
R1, R2, R6: 1K; R_0603_HandSoldering
R3, R4, R5, R7, R8, R9: 10K; R_0603_HandSoldering
SW1: DIP3; OMRON_ELECTRONIC_COMPONENTS_A6S-3102-H_DIP_Switch
U1: TLV1117; SOT-223
U2: CFPS-9-50M
U3: XC9572XL; VQFP44
U4, U6: DLT1111
U5: DLR1111
U7: TLP2704

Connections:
+3V3: C2.2, C3.2, C4.2, C5.1, C6.2, C7.1, C8.1, C9.1, J3.1, J4.1, R4.1, SW1.4, SW1.5, SW1.6, U1.2 (OUT), U2.1 (EN), U2.4 (VDD), U3.15 (VCCINT3.3V), U3.26 (VCCIO2.5V/3.3V), U3.35 (VCCINT3.3V), U4.2 (VCC), U5.3 (VCC), U6.2 (VCC)
+5V: C1.1, C10.1, J2.1, J5.1, P2.1 (VCC), P3.2 (5V), P3.4 (5V), R5.2, U1.3 (IN), U7.6 (VCC)
AXIS_1: R7.2, SW1.1, U3.6 (PIN6)
AXIS_2: R8.2, SW1.2, U3.7 (PIN7)
AXIS_3: R9.2, SW1.3, U3.8 (PIN8)
CLK: U2.3 (OUT), U3.44 (I/O/GCK2)
CRC_ERROR: R6.2, U3.42 (PIN42)
DIR: P4.3, U3.3 (PIN3)
ENABLE: P3.7 (GPIO4), P4.1, U3.5 (PIN5)
EN_LED: R2.2, U3.43 (I/O/GCK1)
ERROR: P4.7, R4.2, U3.1 (I/O/GCK3)
GENERAL1: P3.16 (GPIO23), U3.19 (PIN19)
GENERAL2: P3.18 (GPIO24), U3.18 (PIN18)
GENERAL3: P3.22 (GPIO25), U3.12 (PIN12)
GENERAL4: P3.26 (SPI_CE1_N), U3.41 (PIN41)
GENERAL5: P3.13 (GPIO27), U3.14 (PIN14)
GENERAL6: P3.15 (GPIO22), U3.13 (PIN13)
GND: C1.2, C2.1, C3.1, C4.1, C5.2, C6.1, C7.2, C8.2, C9.2, C10.2, D1.1 (K), D4.1 (K), P1.1, P2.2 (GND), P3.6 (GND), P3.9 (GND), P3.14 (GND), P3.20 (GND), P3.25 (GND), P4.2, P4.4, P4.6, P4.8, P4.10, Q1.2 (S), R3.1, R7.1, R8.1, R9.1, U1.1 (GND), U2.2 (GND), U3.4 (GND), U3.17 (GND), U3.25 (GND), U4.1 (GND), U5.2 (GND), U6.1 (GND), U7.4 (GND)
I2C_SCL: P3.5 (I2C_SCL), U3.22 (PIN22)
I2C_SDA: P3.3 (I2C_SDA), U3.23 (PIN23)
LIMIT: R5.1, U3.38 (PIN38), U7.5 (OUT)
unnamed: D1.2 (A), R2.1
unnamed: D4.2 (A), R6.1
unnamed: J2.2, J3.2, P1.4, R1.1
unnamed: J4.2, J5.2, P4.9
unnamed: P1.2, Q1.3 (D)
unnamed: P1.3, U7.3 (K)
unnamed: R1.2, U7.1 (A)
STEP: P3.11 (GPIO17), P4.5, U3.2 (PIN2)
TCK: P3.23 (SPI_SCK), U3.11 (TCK)
TDI: P3.19 (SPI_MOSI), U3.9 (TDI)
TDO: P3.21 (SPI_MISO), U3.24 (TDO)
TMS: P3.24 (SPI_CE0_N), U3.10 (TMS)
TOLSINK_RX: U3.33 (I/O/GSR), U5.1 (VOUT)
TOSLINK_TX1: U3.32 (PIN32), U6.3 (VIN)
TOSLINK_TX2: U3.34 (I/O/GTS2), U4.3 (VIN)
TRIGGER: P3.12 (GPIO_18), Q1.1 (G), R3.2, U3.37 (PIN37)
UART_RX: P3.8 (UART_TX), U3.21 (PIN21)
UART_TX: P3.10 (UART_RX), U3.20 (PIN20)

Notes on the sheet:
Power Supply Decoupling for CPLD
Axis Selection
Motor Enabled Indication
CRC Error Indication
Place near each CPLD VCC pin !
Main Clock Source For CPLD
Motor Driver Connector
Toslink Transmitter 2
Toslink Receiver
Toslink Transmitter 1
Limit Switch Connection
Power Supply
123 000 - X 001 - Y 010 - Z
Trigger Signal Output

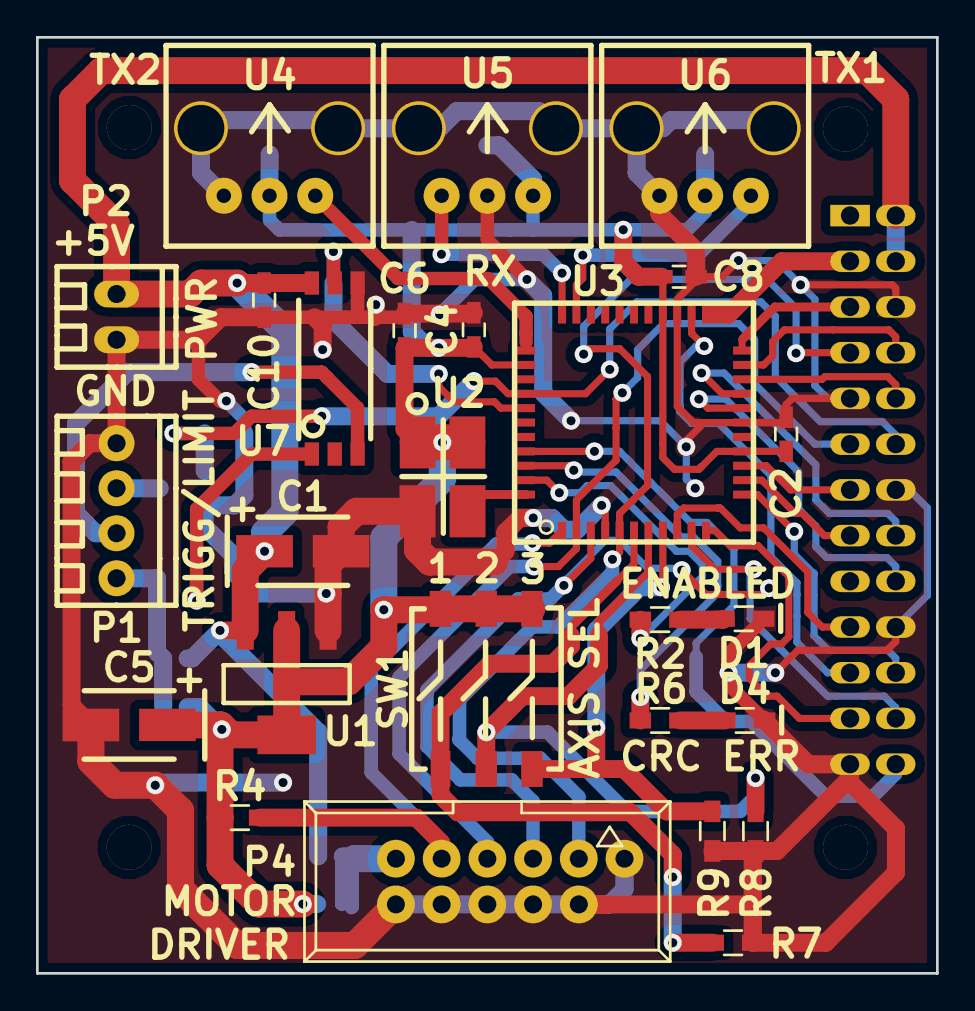
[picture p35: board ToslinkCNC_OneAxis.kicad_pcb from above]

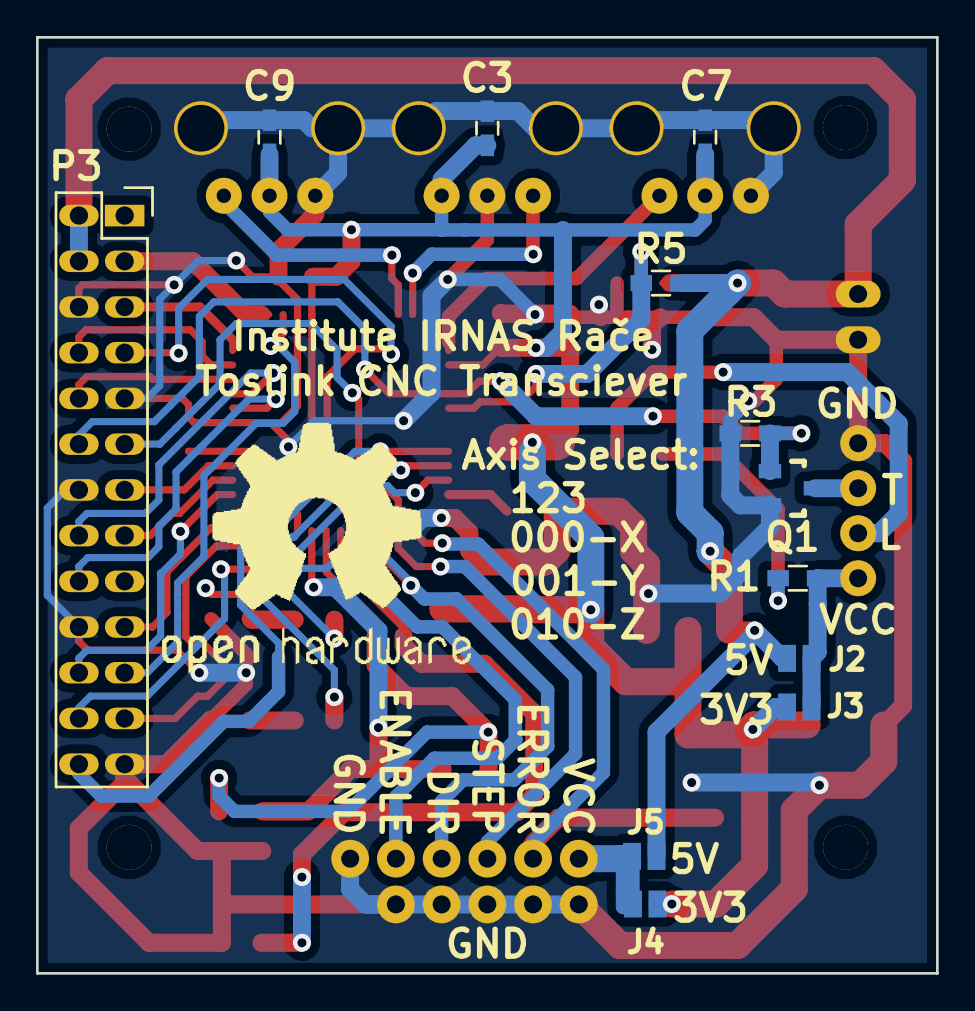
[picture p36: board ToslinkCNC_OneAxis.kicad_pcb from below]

Board: 2 copper layers, 50.0 x 52.0 mm, 38 parts (11 on the bottom side), 39 nets.

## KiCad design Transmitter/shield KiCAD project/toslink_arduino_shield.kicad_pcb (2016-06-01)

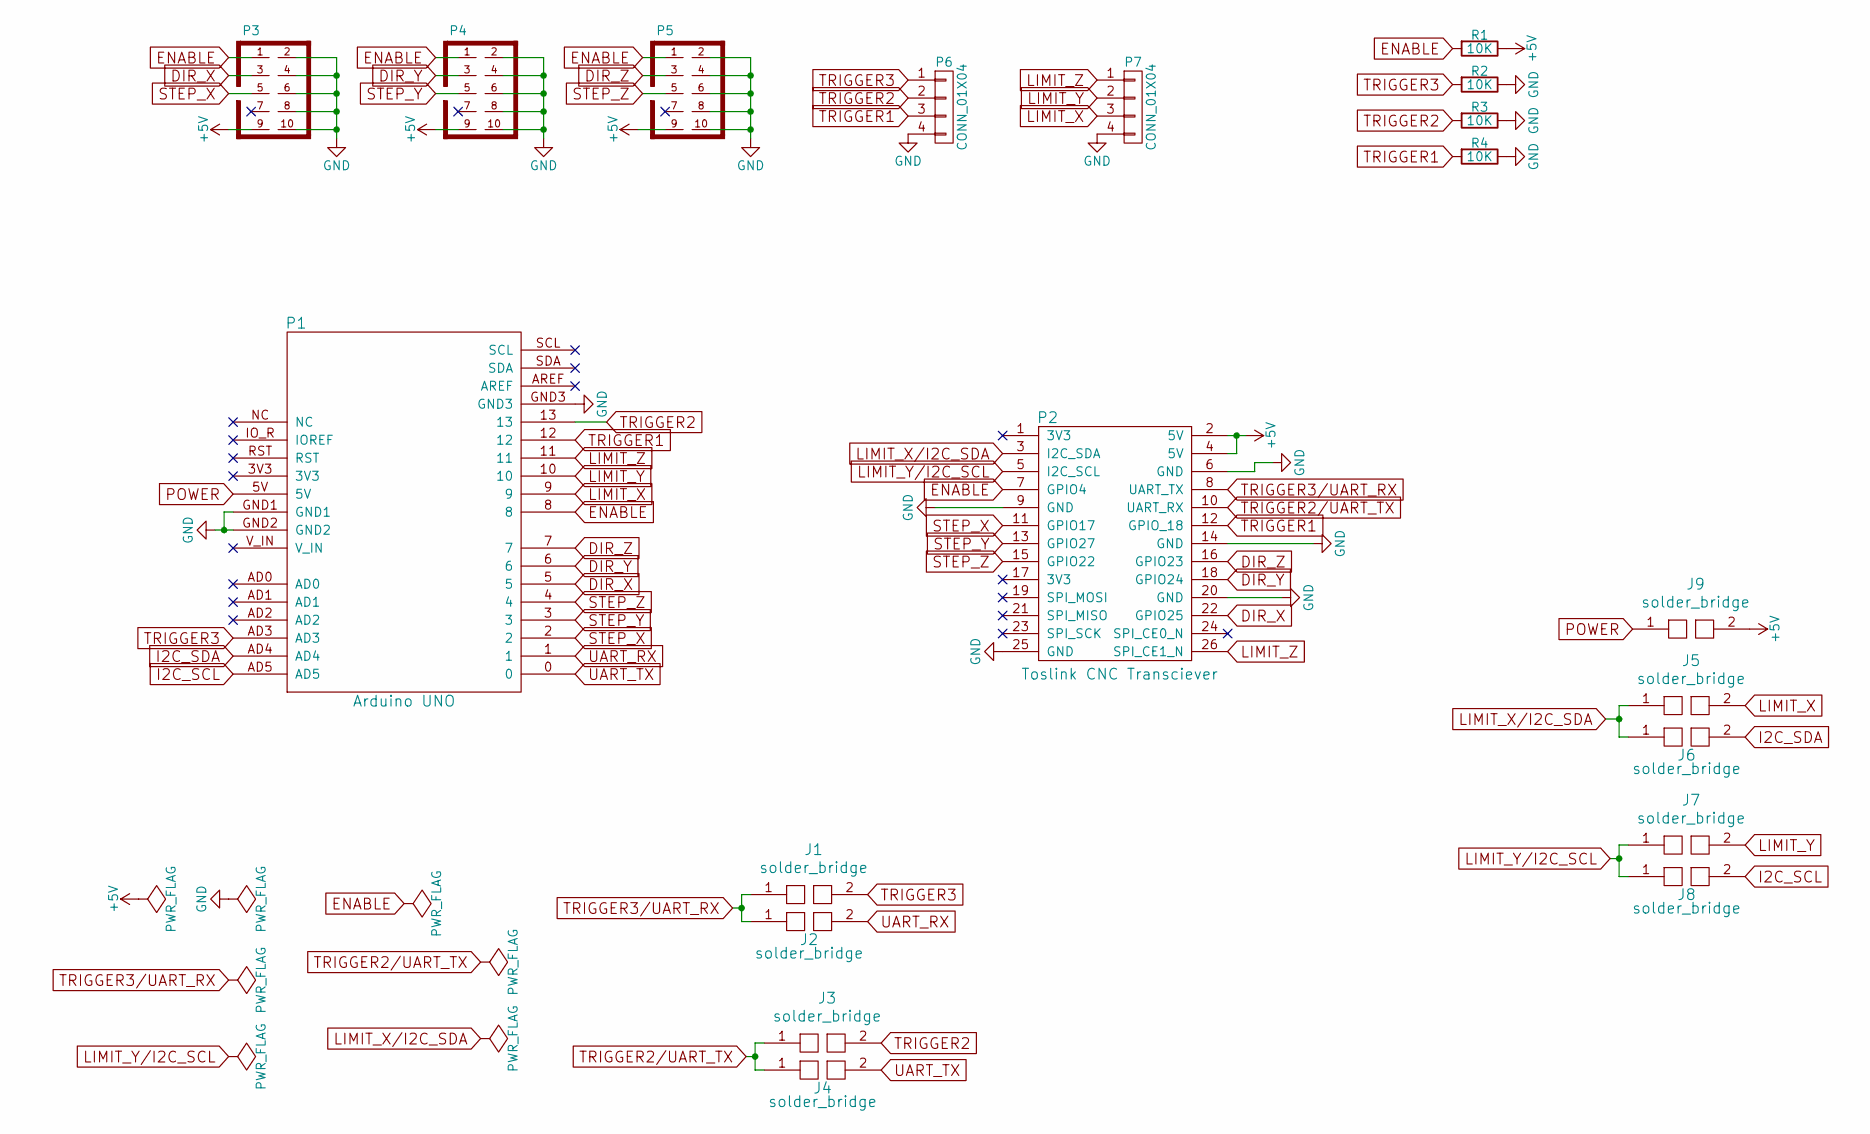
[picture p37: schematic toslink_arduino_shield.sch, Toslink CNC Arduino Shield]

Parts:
J1, J2, J3, J4, J5, J6, J7, J8, J9: solder_bridge
P1: Arduino UNO; ARDUINO_SHIELD
P2: Toslink CNC Transciever; toslink_pcb
P3, P4, P5: PoStep25-32_connector; VASCH5x2
P6, P7: CONN_01X04; terminal_block_2_5mm_4pole
R1, R2, R3, R4: 10K; R_0603_HandSoldering

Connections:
+5V: J9.2, P2.2 (5V), P2.4 (5V), P3.9, P4.9, P5.9, R1.1
DIR_X: P1.5, P2.22 (GPIO25), P3.3
DIR_Y: P1.6, P2.18 (GPIO24), P4.3
DIR_Z: P1.7, P2.16 (GPIO23), P5.3
ENABLE: P1.8, P2.7 (GPIO4), P3.1, P4.1, P5.1, R1.2
GND: P1.GND1, P1.GND2, P1.GND3, P2.6 (GND), P2.9 (GND), P2.14 (GND), P2.20 (GND), P2.25 (GND), P3.2, P3.4, P3.6, P3.8, P3.10, P4.2, P4.4, P4.6, P4.8, P4.10, P5.2, P5.4, P5.6, P5.8, P5.10, P6.4, P7.4, R2.1, R3.1, R4.1
I2C_SCL: J8.2, P1.AD5
I2C_SDA: J6.2, P1.AD4
LIMIT_X: J5.2, P1.9, P7.3
LIMIT_X/I2C_SDA: J5.1, J6.1, P2.3 (I2C_SDA)
LIMIT_Y: J7.2, P1.10, P7.2
LIMIT_Y/I2C_SCL: J7.1, J8.1, P2.5 (I2C_SCL)
LIMIT_Z: P1.11, P2.26 (SPI_CE1_N), P7.1
POWER: J9.1, P1.5V
STEP_X: P1.2, P2.11 (GPIO17), P3.5
STEP_Y: P1.3, P2.13 (GPIO27), P4.5
STEP_Z: P1.4, P2.15 (GPIO22), P5.5
TRIGGER1: P1.12, P2.12 (GPIO_18), P6.3, R4.2
TRIGGER2: J3.2, P1.13, P6.2, R3.2
TRIGGER2/UART_TX: J3.1, J4.1, P2.10 (UART_RX)
TRIGGER3: J1.2, P1.AD3, P6.1, R2.2
TRIGGER3/UART_RX: J1.1, J2.1, P2.8 (UART_TX)
UART_RX: J2.2, P1.1
UART_TX: J4.2, P1.0

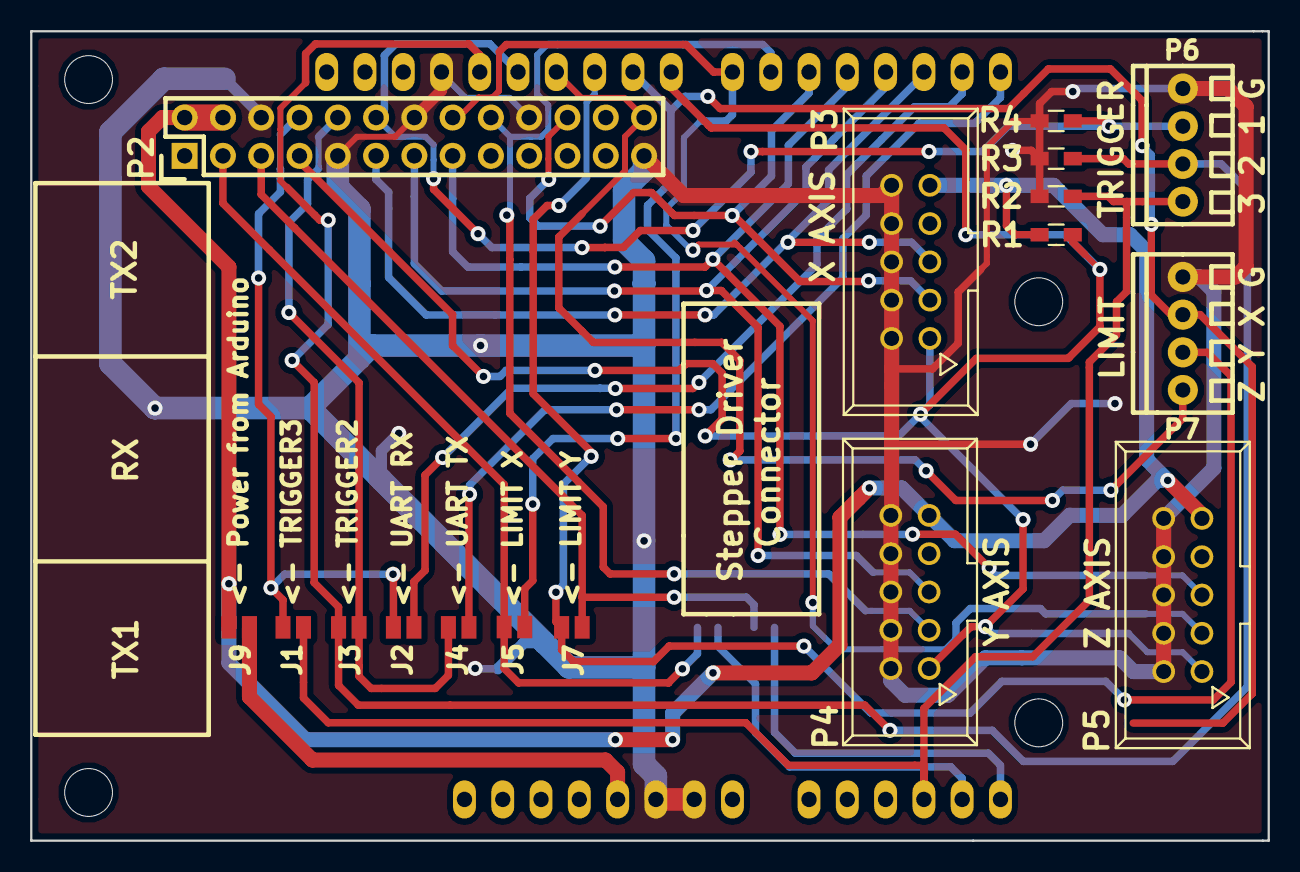
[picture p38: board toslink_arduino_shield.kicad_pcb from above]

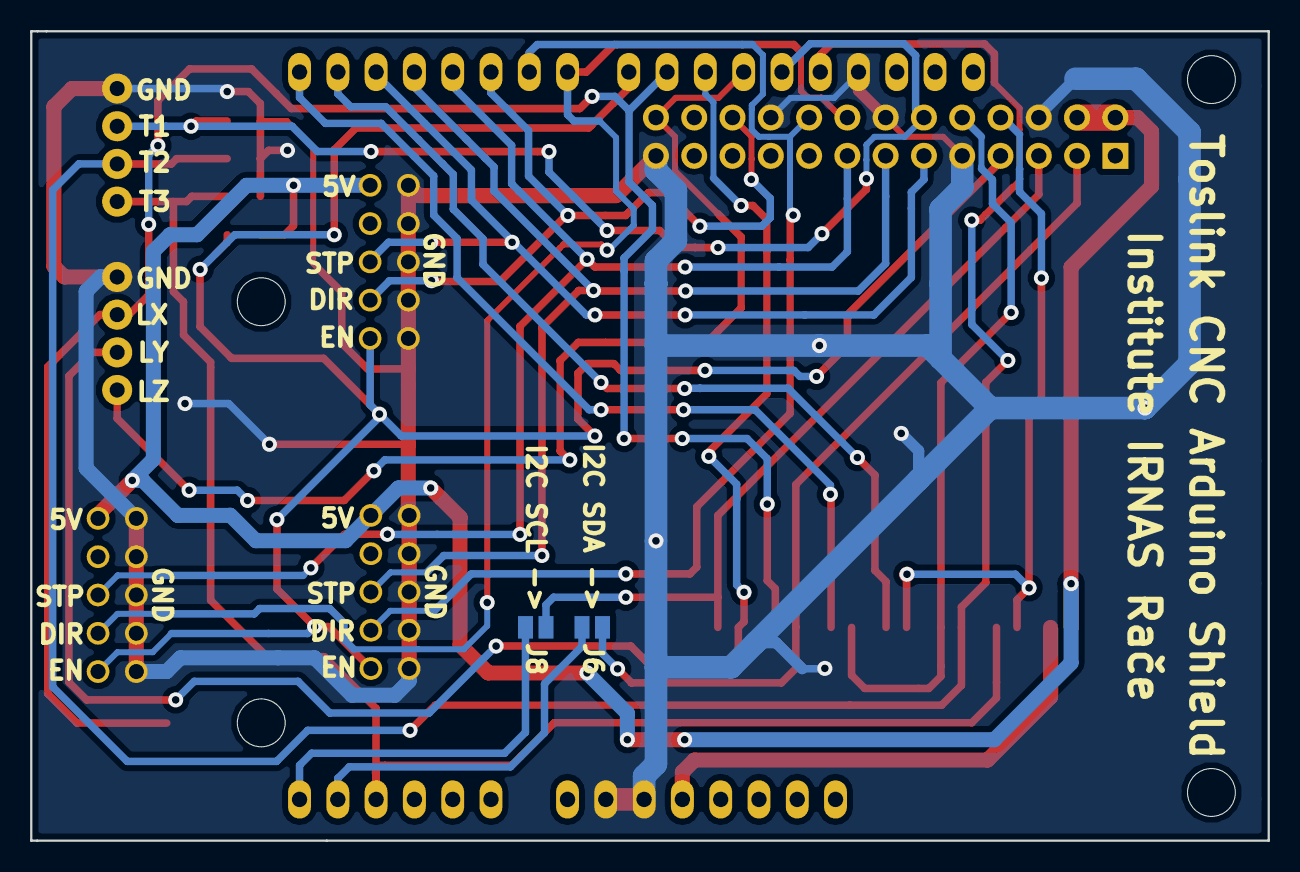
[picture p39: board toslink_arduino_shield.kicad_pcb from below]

Board: 2 copper layers, 82.1 x 53.7 mm, 20 parts (2 on the bottom side), 24 nets.

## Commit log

2016-03-02 Toslink Transmitter Update
    [shield BOM.ods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]
2016-03-10 Releasing the system
    [ToslinkCNC_OneAxis.kicad_pcb, ToslinkCNC_OneAxis.sch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]
2016-10-21 Added Toslink CNC To PlanetCNC ECO Shield
    [Toslink PlanetCNC ECO shield.sch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]
2016-10-21 Added Planet CNC ECO Shield BOM
    [Planet CNC shield BOM.ods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]
